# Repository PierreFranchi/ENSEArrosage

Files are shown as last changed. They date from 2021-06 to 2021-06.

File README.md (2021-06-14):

# ENSEArrosage
Projet de première année à l'ENSEA

Projet 1ère Année à l’ENSEA

Présentation du projet :

Le but de ce projet est de créer un système permettant d’automatiser l’arrosage des 2 murs végétalisés disposés dans la K-fet de l'Ensea.

Pour cela nous disposons de 3 capteurs : un de température et d’humidité de l’air, un de luminosité et un autre mesurant l'humidité du sol. Ces 3 capteurs sont reliés à une STM32, qui elle-même communique avec une Raspberry Pi.
De plus, la Raspberry Pi récupère des données météorologiques depuis une API météo.
Pour finir, un site web, hébergé sur la RPI, permet d’observer en temps réel les données des capteurs et celles provenant de l’API météo mais aussi de contrôler le type d'arrosage des plantes. Ainsi, deux modes sont disponibles : 
- un mode manuel : L’utilisateur peut entrer sur le site une durée d’arrosage. 
- un mode automatique : L’arrosage est géré intelligemment en fonction des données des capteurs et de la météo des jours à venir.

L’acquisition des données météos et des données des capteurs s’effectuent une fois toutes les  6h.

De plus nous devons répondre au cahier des charges suivant :
- Utiliser une RPI
- Disposer de 3 types de capteurs : humidité, luminosité et température
- Travailler avec les données météorologiques en temps réel (API Météo)
- Créer un serveur WEB afin de vérifier l’état du plant et contrôler manuellement l’arrosage.
- Contrôler l’arrivée d’eau

Pour plus de détails, un diaporama de présentation est présent dans le GIT.

Liste du matériel :

- Raspberry pi 4 
- STM32-L476 nucleo
- Capteur Température + Humidité : DHT22 (AM2302)
- Capteur Luminosité : Grove Light Sensor
- Capteur Humidité : Grove Moisture Sensor
- Régulateur de tension 78L05F
- 2 Condensateurs 865060645008 WÜRTH ELEKTRONIK

Liste des logiciels utilisés :

- CUBEIDE pour le code en C
- Eagle pour le schéma électrique et  le PCB
- VS code pour programmer en python, CSS, HTML et SQL

Présentation du contenu du GIT : 

Ce GIT est composé de plusieurs fichiers : 

- Un script bash
- Un dossier comprenant le code en C que nous avons développé sous CubeIDE.
- Un dossier comprenant un site web codé en HTML et en CSS qui nous permet de contrôler l’arrosage et deux codes en python, un pour récupérer les valeurs des capteurs et les données météos et un autre pour lancer le site web.
- Le schéma et le PCB (et la librairie qui va avec) de la carte que nous avons produite.
- Le diaporama que nous avons utilisé pour faire notre présentation.

Tutoriel d’installation :

- Commencer par démarrer la raspberry et la connecter à Internet
- Là, il y a deux options : soit lancer  le script bash afin qu'il télécharge le projet et l'exécute, soit télécharger le projet en entier depuis github
- Faire le montage électrique en suivant le schéma
- Upload le code qui est sur CUBEIDE sur la STM32

NB : Comme l’UART côté RPI ne fonctionnait pas, on a préféré ne pas mettre les commandes d’installation dans le script bash car ce sont peut-être elles qui causent  ce dysfonctionnement.

NB2 : On a décidé d’anonymiser le projet ou cas où il serait rendu public.

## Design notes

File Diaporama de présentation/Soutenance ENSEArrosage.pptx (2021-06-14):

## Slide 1

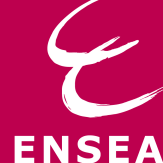
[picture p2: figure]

PROJET 1ère ANNEE

ENSEArrosage

11 juin 2021

## Contexte et Objectifs

But : automatiser l’arrosage d’un espace vert

- Définir le cahier des charges
- Gérer l'avancement du projet (GANTT)
- Réaliser un PCB
- Communiquer

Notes: Ce projet consiste à automatiser l’arrosage des plantes dans la K-fet de l’ENSEA.

## DIAGRAMME

Alimentation

Raspberry

Capteurs

Site Web

STM32

Eau

Données météo

Plantes

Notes: Nous utiliserons une carte STM32 alimenté par le réseau qui permettra de contrôler des capteurs qui mesureront l’humidité de la terre dans les pots des plantes, l’humidité de l’air, la température et l’éclairement des plantes. Avec ces données et les données météorologiques récupérés par une API (application programming interface), elle même commandé par une carte raspberry, les plantes seront arrosé ou non. Un site Web permet de contrôler et commander a distance ce système .

## Planning Gantt

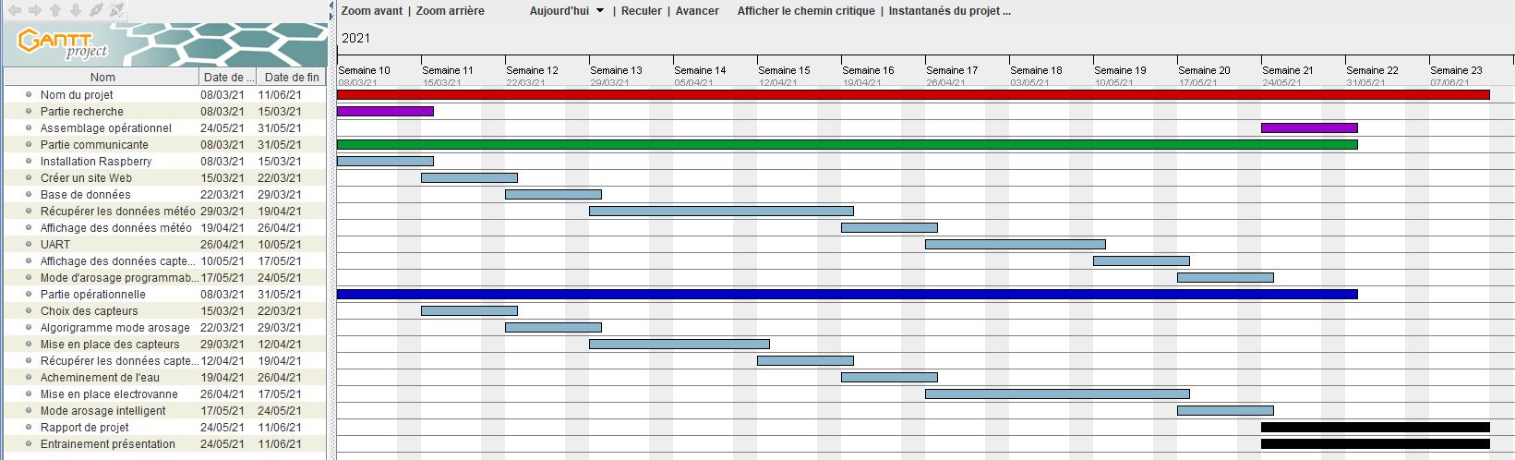
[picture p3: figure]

ENSEArrosage

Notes: Nous avons listé les tâches à réaliser et planifier le tout dans le temps à l’aide d’un planning Gantt. Cela nous a permis de voir l’avancement du projet.

## Choix Capteurs

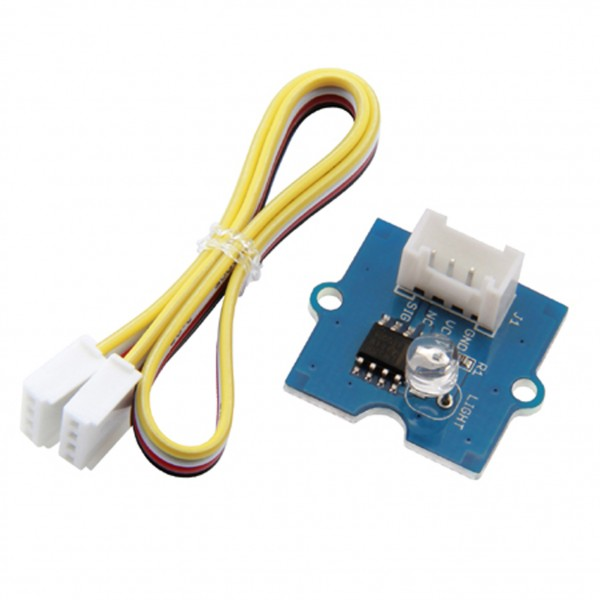
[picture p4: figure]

Capteur luminosité

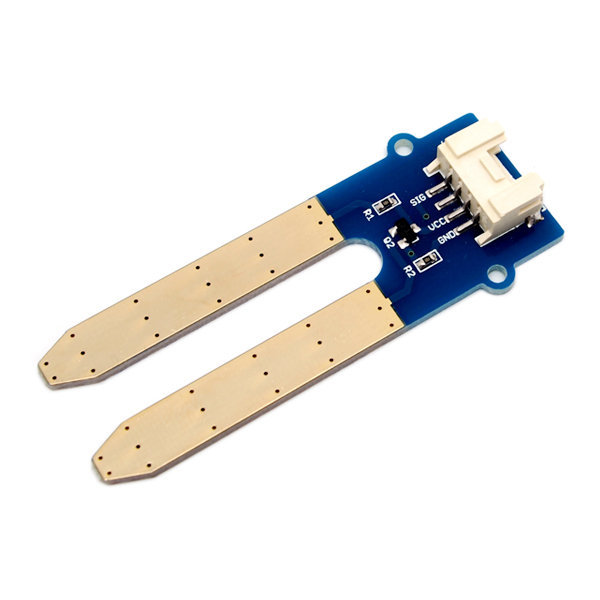
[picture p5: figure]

Capteur d’humidité

Critère de sélection :
-Pertinence
-Alimentation
-Compatibilité

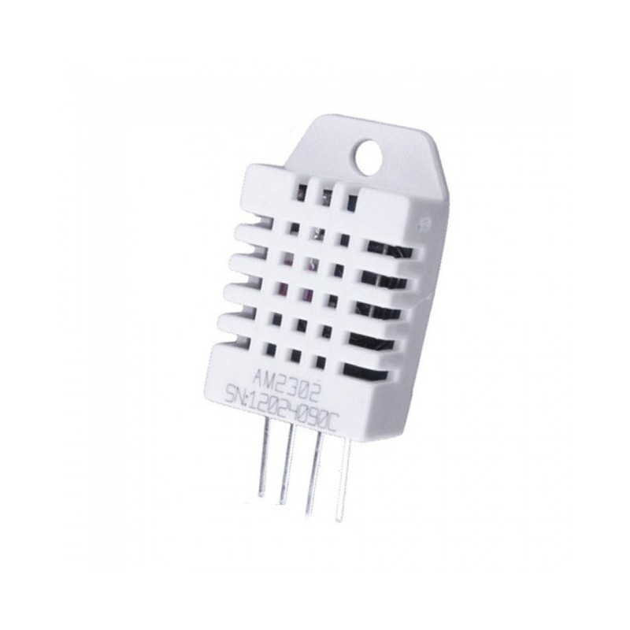
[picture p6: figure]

Capteur température

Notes: Capteurs au fonctionnement TRÈS simple :
Conductivité du sol
Photorésistance

Choix Capteurs :
Résolution, Plage de mesures, Alimentation, Type de données, Compatibilité, Prix

Disponibilité :

## Montage Électrique

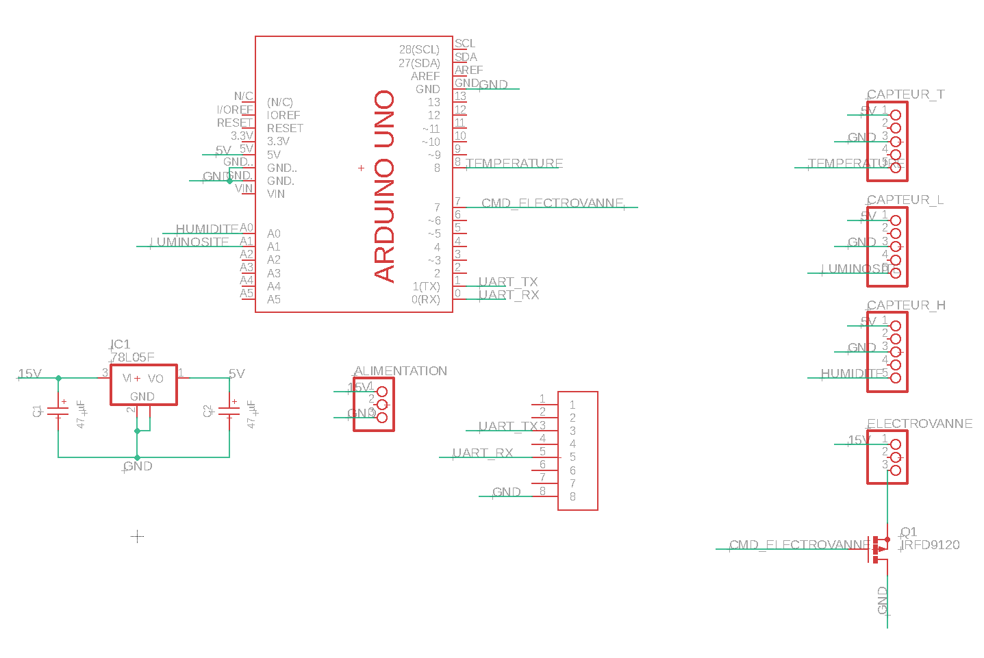
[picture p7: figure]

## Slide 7

Fonctionnement global

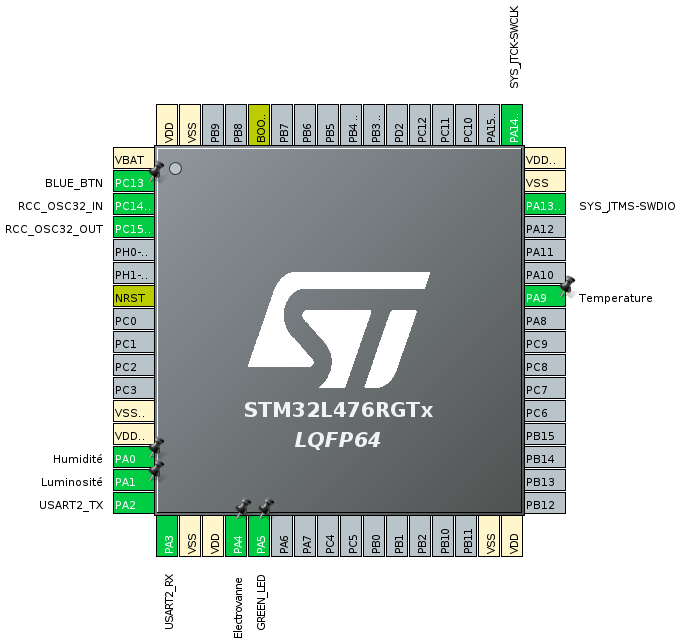
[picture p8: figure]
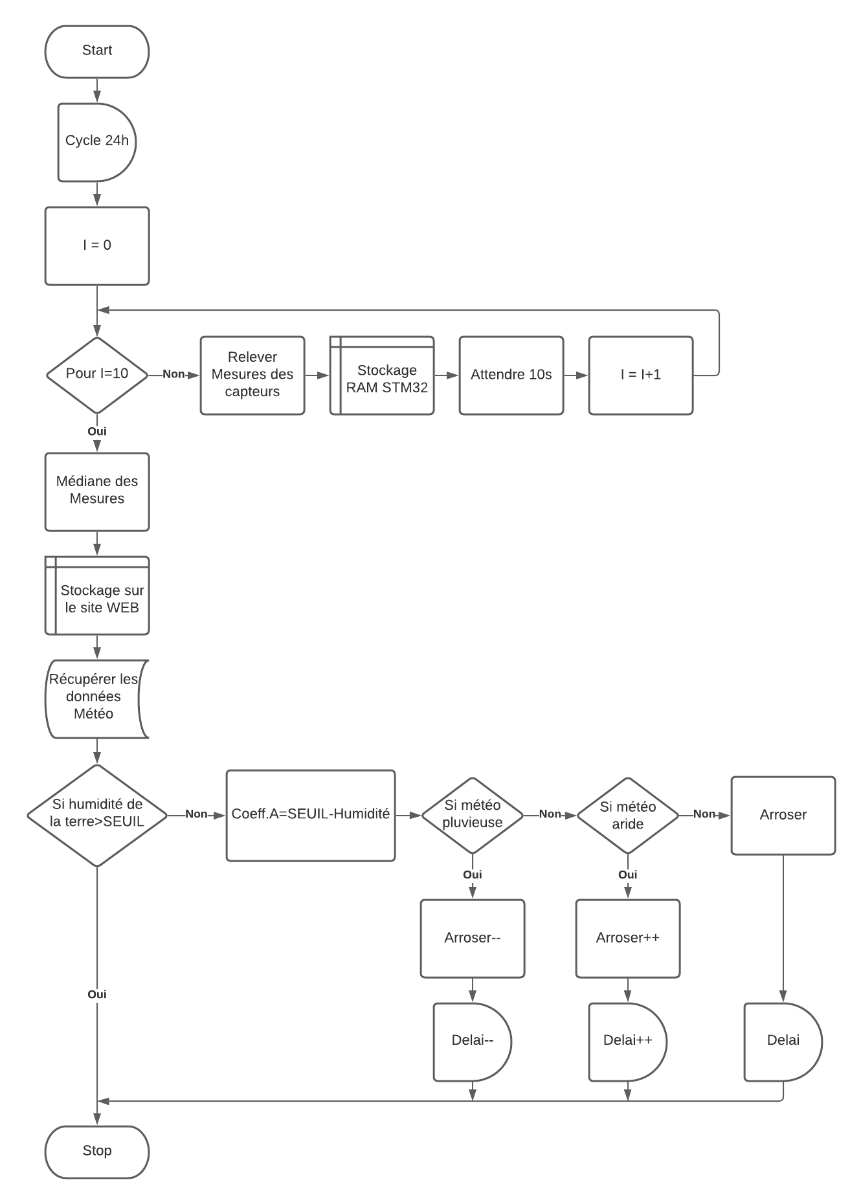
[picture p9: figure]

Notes: Algorigramme (10 mesures + seuil d’arrosage)
On a configuré les entrée sorties, avec de l’analogique pour les capteurs

On utilise un Dma (direct memory access) pour récupérer la valeur des capteur directement dans la mémoire interne. Lorsque l’on veut prendre une mesure on active une interruption, le capteur récupère la valeur, puis le processeur peut réaliser une autre tâche. Cela permet de limiter l’activité du processeur donc de conserver la fluidité d’utilisation.

## Tests Capteurs

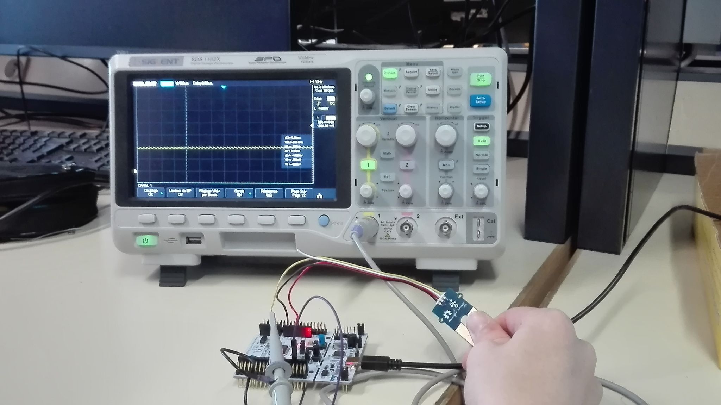
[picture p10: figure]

Vérification du bon fonctionnement des capteurs

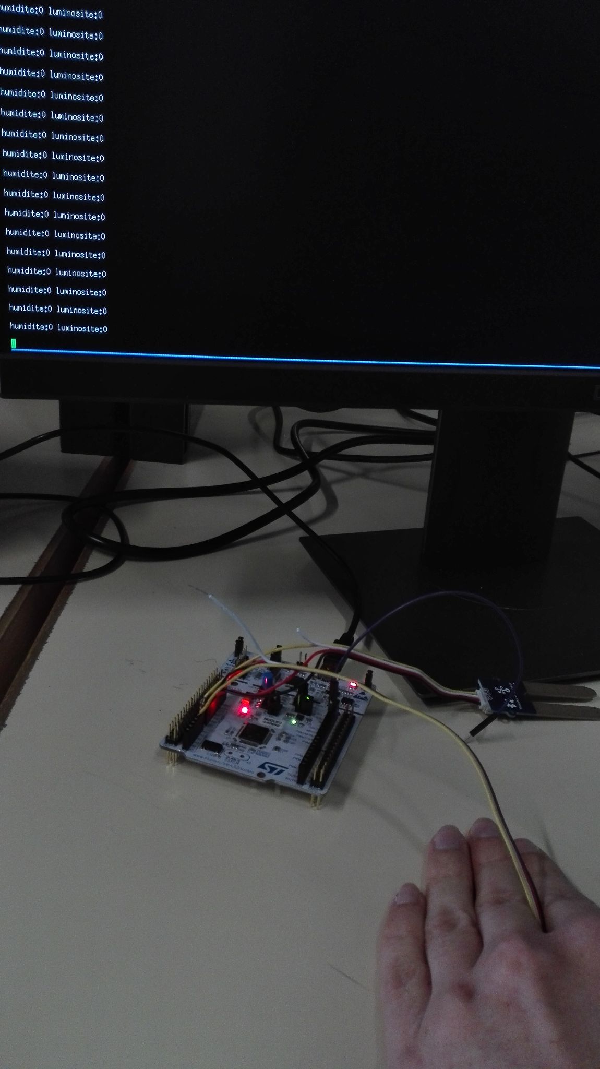
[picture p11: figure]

Absence de luminosité et humidité de l’air

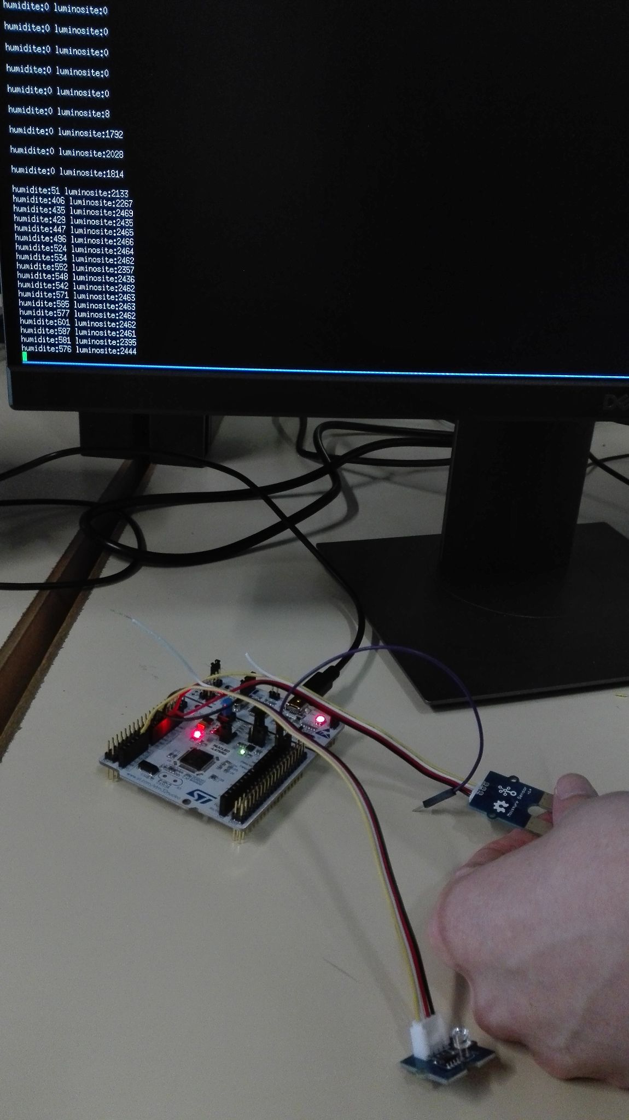
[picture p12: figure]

Luminosité de la salle et simulation d’humidité

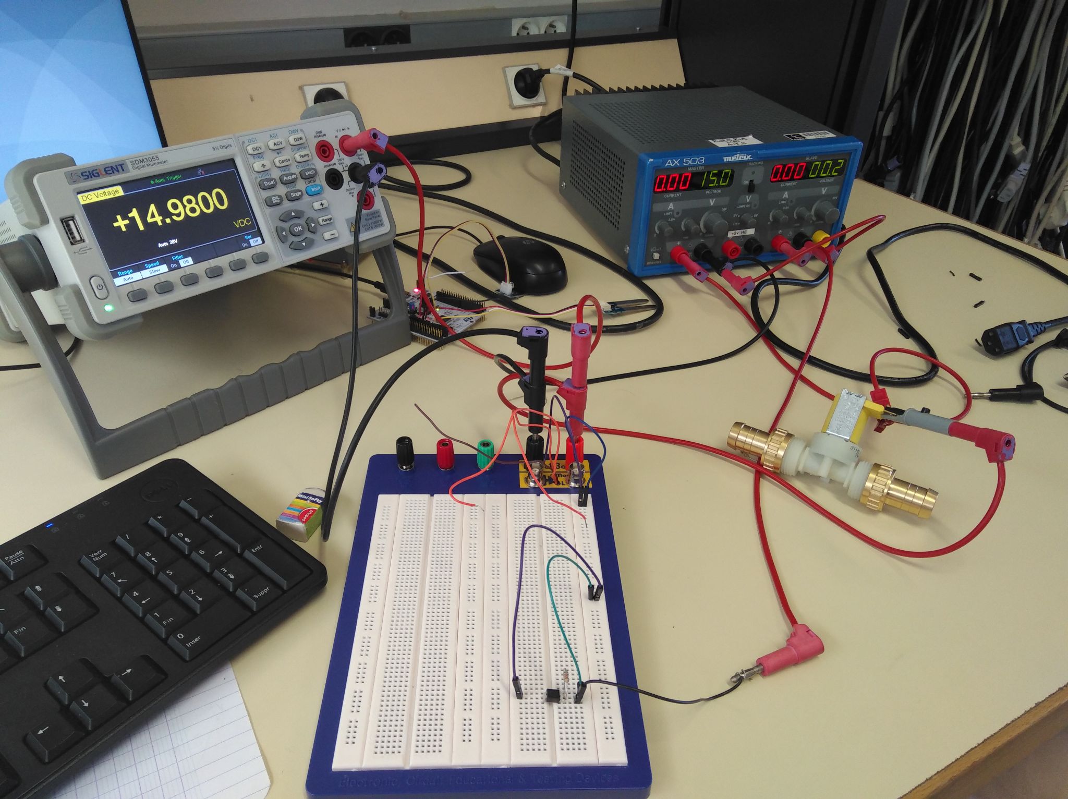
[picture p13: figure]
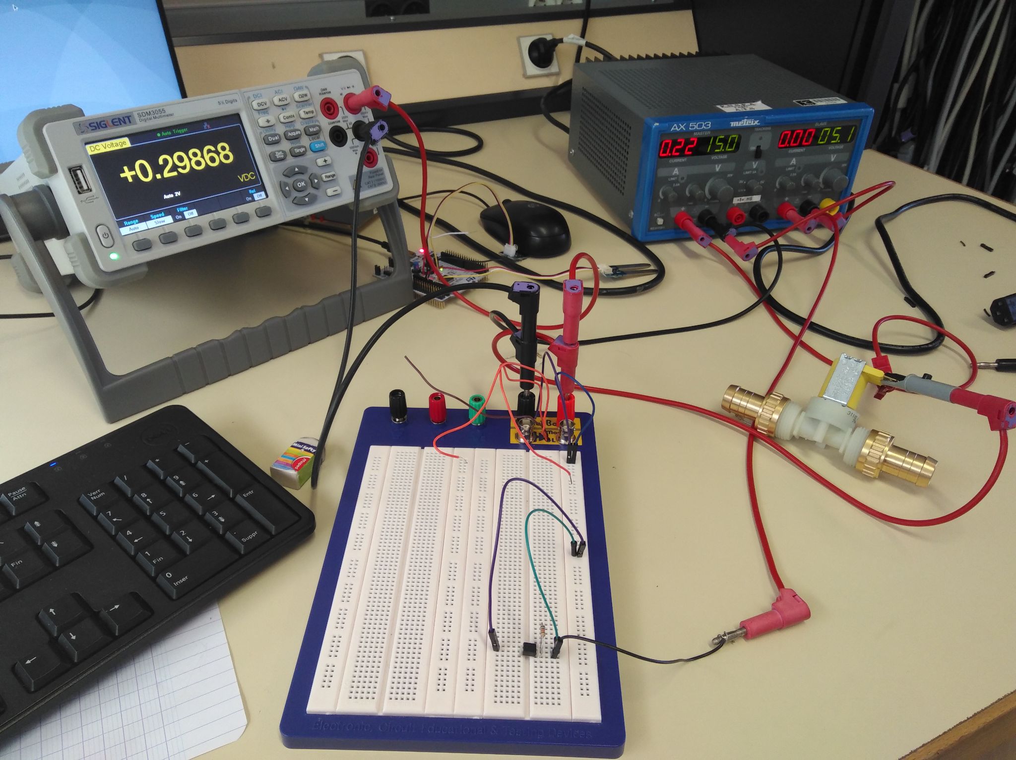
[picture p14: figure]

Vérification du bon fonctionnement de l'électrovanne
Celle-ci est ouverte quand le transistor est passant.

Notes: Nous avons vérifié le bon fonctionnement des capteurs à l’aide d’un oscilloscope et celui de l'électrovanne.
Après l’écriture du code sur CubeIDE pour contrôler les capteurs nous avons pu observer leurs bon fonctionnement. Nous observons une variation des valeurs en cachant ou en laissant exposé le capteur de luminosité et en reliant les bornes du capteur d’humidité avec nos doigts pour simuler la terre.

Expérience des tests

## DIAGRAMME

BDD

STM32

commande

capteurs

SQL

UART

historique + données

données météo

python

Raspberry Pi

affichage

commande de l’arrosage

HTML

API

site web

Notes: Serveur flask

## Récupération de la météo et des données capteurs

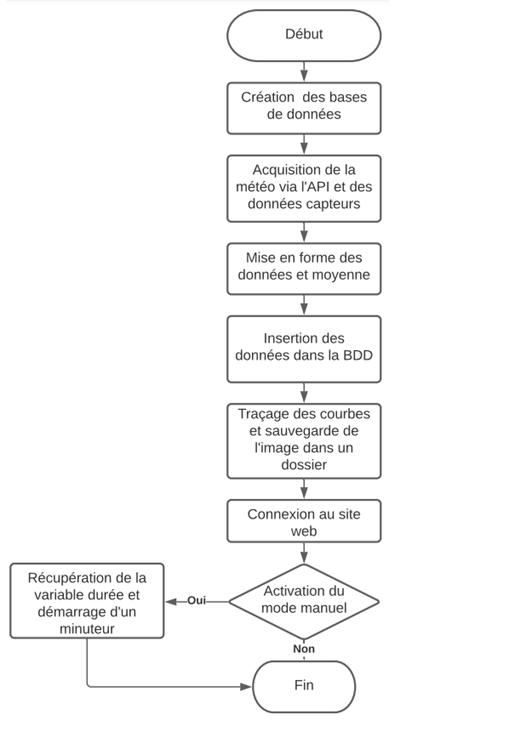
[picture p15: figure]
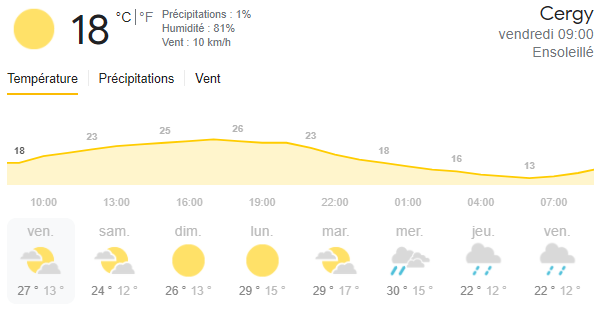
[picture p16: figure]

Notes: Concernant la récupération des données, deja on récupère deux types de données, la météo donc la température , l humidité et le temps qu’l fait des 3 prochains jours, ainsi que les données des capteurs recu de la STM. on a créé deux bases de données dans laquelle on stocke les valeurs de chaque capteur que la STM32 nous a envoyé
Comme l’API nous donne beaucoup d’informations, on fait d’abord une moyenne, puis on stocke tout dans une base de données. Que l’on utilisera par la suite pour savoir si l’on doit arroser ou non.

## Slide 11

Site WEB

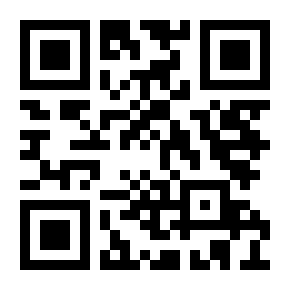
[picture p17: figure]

présentation du projet

données météo

historique

commande

navigation

## Conclusion

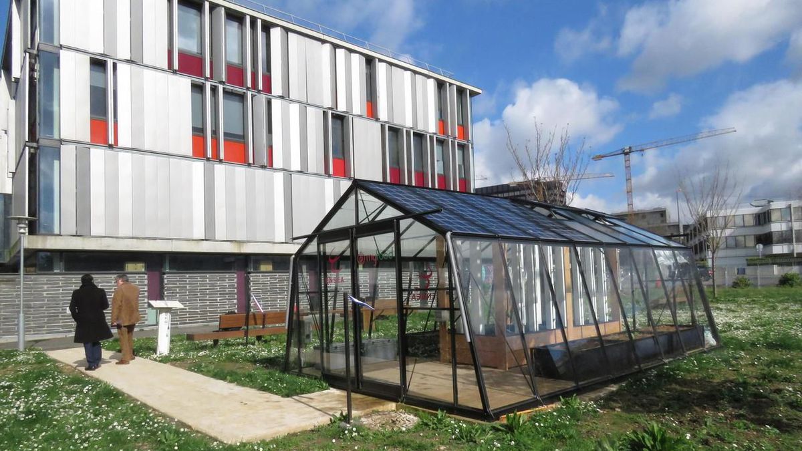
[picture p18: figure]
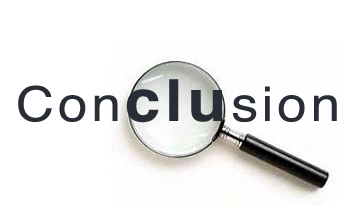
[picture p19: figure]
Conclusion de l&#39;enquête terrain – Quelle reconnaissance professionnelle pour les MOOC ?

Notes: Pour conclure, nous avons réalisé le PCB et la totalité des schémas électriques .Nous avons aussi 2 capteurs qui récupèrent des mesures d’humidité de la terre et de luminosité. La partie acquisition des données est entièrement faite avec le stockage dans les bases de données. Le site est opérationnel, il nous affiche l’historique des mesures des capteurs et la possibilité de changer de mode d’arrosage.

Avec plus de temps nous aurions pu continuer la communication UART, qui fonctionne côté STM32, mais pas côté RPI et l’affichage de la météo sur le site.

Il aurait aussi fallu paramétrer le dernier capteur afin de mesurer la température et l’humidité de l’air. Celui-ci est un capteur numérique, il nécessite l’utilisation d’autres outils sur CubeIDE. Il aurait fallu étalonner les capteurs et définir des seuils précis dans lesquels il faut arroser ou attendre et écrire le code pour contrôler l'électrovanne.

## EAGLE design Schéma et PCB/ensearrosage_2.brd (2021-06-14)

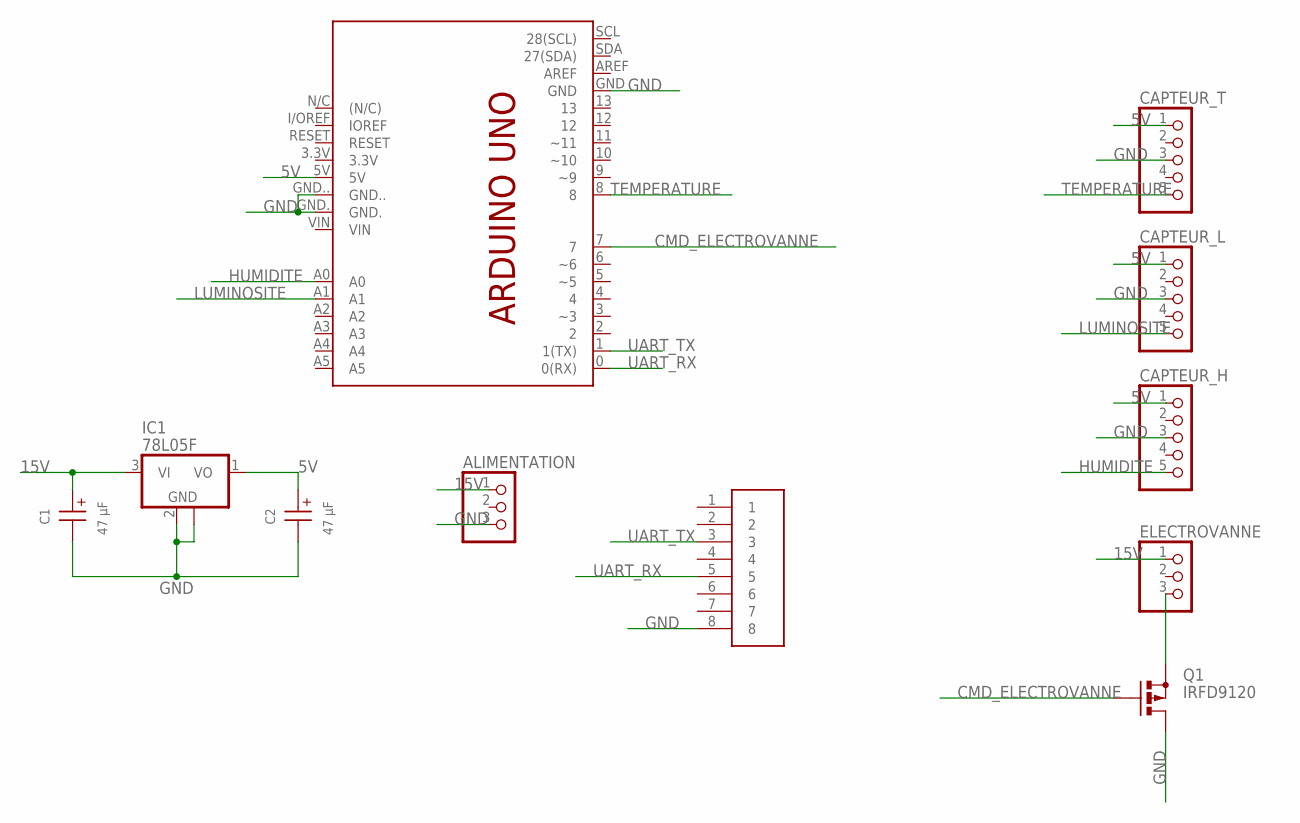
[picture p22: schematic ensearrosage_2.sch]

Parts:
ALIMENTATION: PINHD-1X3; 1X03
C1, C2: 47 µF; WCAP-ASLI_5X5.5(DXL)
CAPTEUR_H: PINHD-1X5; 1X05
CAPTEUR_L: PINHD-1X5; 1X05
CAPTEUR_T: PINHD-1X5; 1X05
ELECTROVANNE: PINHD-1X3; 1X03
IC1: 78L05F; SOT89
PCB1: ARDUINO_UNO
Q1: IRFD9120; C370-01
U$2: RJ45

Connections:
5V: C2.1 (+), CAPTEUR_H.1, CAPTEUR_L.1, CAPTEUR_T.1, IC1.1 (VO), PCB1.5V
15V: ALIMENTATION.1, C1.1 (+), ELECTROVANNE.1, IC1.3 (VI)
CMD_ELECTROVANNE: PCB1.7, Q1.G
GND: ALIMENTATION.3, C1.2 (-), C2.2 (-), CAPTEUR_H.3, CAPTEUR_L.3, CAPTEUR_T.3, IC1.2 (GND), IC1.2@1 (GND), PCB1.GND, PCB1.GND., PCB1.GND.., Q1.D, Q1.D1 (D), U$2.8
HUMIDITE: CAPTEUR_H.5, PCB1.A0
LUMINOSITE: CAPTEUR_L.5, PCB1.A1
unnamed: ELECTROVANNE.3, Q1.S
TEMPERATURE: CAPTEUR_T.5, PCB1.8
UART_RX: PCB1.0 (0(RX)), U$2.5
UART_TX: PCB1.1 (1(TX)), U$2.3

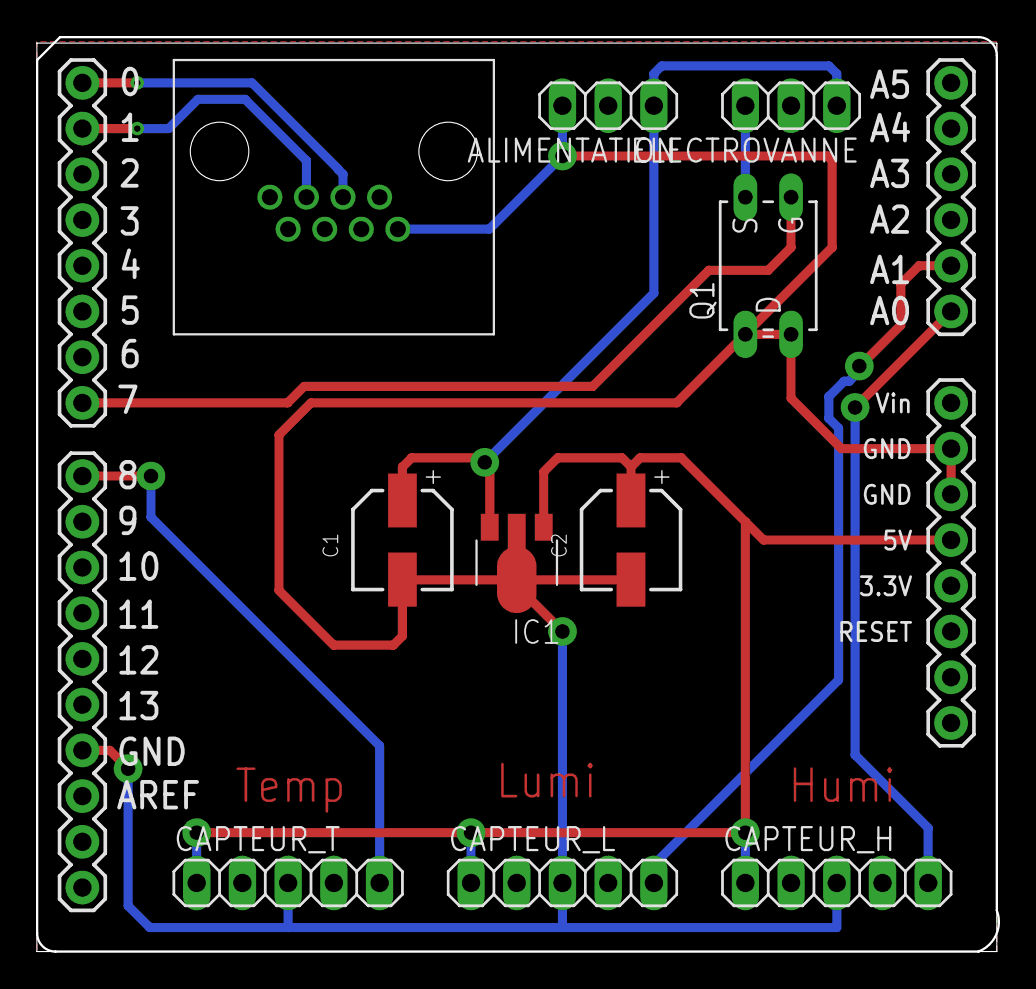
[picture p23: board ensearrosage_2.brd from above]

Board: 2 copper layers, 53.4 x 50.8 mm, 11 parts (0 on the bottom side), 10 nets.

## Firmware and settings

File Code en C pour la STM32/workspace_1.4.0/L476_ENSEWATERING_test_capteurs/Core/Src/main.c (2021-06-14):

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
/* Includes ------------------------------------------------------------------*/
#include "main.h"

/* USER CODE BEGIN Includes */
#include <stdint.h>				// déclaration des bibliothèques
#include <stdio.h>
/* USER CODE END Includes */

ADC_HandleTypeDef hadc1;		// on nomme les signaux
DMA_HandleTypeDef hdma_adc1;

TIM_HandleTypeDef htim1;

UART_HandleTypeDef huart2;

/* USER CODE BEGIN PV */
uint16_t humidite,luminosite;	// déclaration de humidite et luminosite comme des entiers sur 16 bits
uint16_t table[2];

uint8_t it_adc;
char UART_TX_BUFFER[32];
/* USER CODE END PV */

void SystemClock_Config(void);	// on configure l'horloge
static void MX_GPIO_Init(void);
static void MX_DMA_Init(void);
static void MX_USART2_UART_Init(void);
static void MX_ADC1_Init(void);
static void MX_TIM1_Init(void);
/**
  * @brief  The application entry point.
  * @retval int
  */
int main(void)
{
  /* MCU Configuration--------------------------------------------------------*/

  /* Reset of all peripherals, Initializes the Flash interface and the Systick. */
  HAL_Init();

  /* Configure the system clock */
  SystemClock_Config();

  /* Initialize all configured peripherals */
  MX_GPIO_Init();
  MX_DMA_Init();
  MX_USART2_UART_Init();
  MX_ADC1_Init();
  MX_TIM1_Init();
  /* USER CODE BEGIN 2 */
  HAL_ADC_Start_DMA(&hadc1, table, 2);  // table[0]= humidité; table[1]=luminosité
  HAL_TIM_Base_Start(&htim1);

  it_adc = 0;					// on fixe it_adc à 0

  sprintf(UART_TX_BUFFER,"Starting... \r\n", table[0],table[1]);  //
  HAL_UART_Transmit(&huart2, UART_TX_BUFFER, 32, HAL_MAX_DELAY);  //
  /* USER CODE END 2 */

  /* Infinite loop */
  /* USER CODE BEGIN WHILE */




  while (1)
  {
	  if(it_adc){      		// lorsqu'il y a une interruption, it_adc = 1, on exécute la condition
		  // Votre code à faire à la réception de données


		  //table[0]= humidite;
		  //table[1]= luminosite;
		  sprintf(UART_TX_BUFFER,"humidite:%d luminosite:%d\r\n", table[0],table[1]); // on affiche les signaux sur la console, utile uniquement pour les tests
		  HAL_UART_Transmit(&huart2, UART_TX_BUFFER, 32, HAL_MAX_DELAY) 	;      // on envoie les valeurs d'humidité et de luminosité a la raspberry


		  it_adc = 0;    // on remet it_adc à 0 et on attend la prochaine interruption
	  }
	  HAL_GPIO_TogglePin(GREEN_LED_GPIO_Port, GREEN_LED_Pin); //atteste du fonctionnement de la carte



	  /*  HAL_ADC1_ReadPin(humidité_sol);  */

    /* USER CODE END WHILE */

    /* USER CODE BEGIN 3 */
  }
  /* USER CODE END 3 */
}

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
/* USER CODE BEGIN 4 */
void HAL_ADC_ConvCpltCallback(ADC_HandleTypeDef * hadc1){
	it_adc = 1;
}
/* USER CODE END 4 */
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


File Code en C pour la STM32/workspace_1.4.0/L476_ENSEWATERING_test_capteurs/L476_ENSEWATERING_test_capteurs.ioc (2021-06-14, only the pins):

Mcu.UserName=STM32L476RGTx
PA0.GPIO_Label=Humidit\u00E9
PA0.Signal=ADCx_IN5
PA1.GPIO_Label=Luminosit\u00E9
PA1.Signal=ADCx_IN6
PA2.Signal=USART2_TX
PA3.Signal=USART2_RX
PA4.GPIO_Label=Electrovanne
PA4.Signal=GPIO_Output
PA5.GPIO_Label=GREEN_LED
PA5.Signal=GPIO_Output
PA9.GPIO_Label=Temperature
PA9.Signal=GPIO_Input
PC13.GPIO_Label=BLUE_BTN
PC13.Signal=GPIO_Input

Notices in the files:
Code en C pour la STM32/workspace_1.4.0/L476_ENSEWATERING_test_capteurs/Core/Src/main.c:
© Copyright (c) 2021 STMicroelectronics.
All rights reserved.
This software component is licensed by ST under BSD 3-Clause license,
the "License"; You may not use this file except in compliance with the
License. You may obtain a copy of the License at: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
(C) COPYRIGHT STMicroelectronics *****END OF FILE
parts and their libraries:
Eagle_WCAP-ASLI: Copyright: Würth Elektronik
